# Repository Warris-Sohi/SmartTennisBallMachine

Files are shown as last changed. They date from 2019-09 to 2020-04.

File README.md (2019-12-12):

# SmartTennisBallMachine
warris-sohi.github.io/SmartTennisBallMachine
## Table of Contents
[Introduction](https://github.com/Warris-Sohi/SmartTennisBallMachine#Introduction)

[Build Materials](https://github.com/Warris-Sohi/SmartTennisBallMachine#Materials-Required)

[Time Commitment](https://github.com/Warris-Sohi/SmartTennisBallMachine#Time-Commitment)

[Quick Links](https://github.com/Warris-Sohi/SmartTennisBallMachine#Quick-Links) 

[Testing the acquired materials](https://github.com/Warris-Sohi/SmartTennisBallMachine#Step-1-Test-the-acquired-materials)

[Testing the breadboard prototype.](https://github.com/Warris-Sohi/SmartTennisBallMachine#Step-2-Testing-the-breadboard-prototype)

[Build a PCB prototype](https://github.com/Warris-Sohi/SmartTennisBallMachine#Step-3-Build-a-PCB-prototype)

[Lasercut case and Assembling](https://github.com/Warris-Sohi/SmartTennisBallMachine#Step-4-Project-Enclosure)

[Production Testing](https://github.com/Warris-Sohi/SmartTennisBallMachine#Step-4-Project-Enclosure)

[Conclusion](https://github.com/HusnalK/Resistor-Value-Recognizer-RVR#Conclusion)
## Introduction
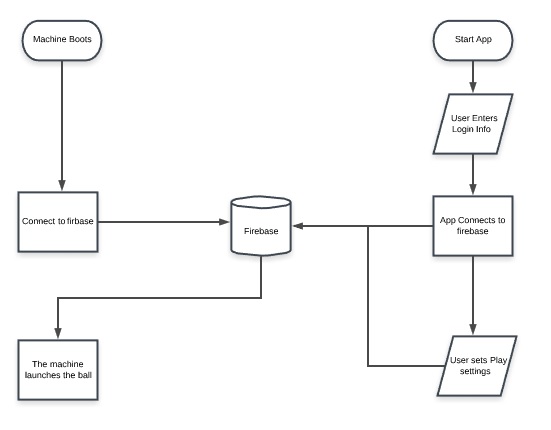
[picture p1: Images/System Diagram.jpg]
System Diagram

##### These instructions are provided to build a launcher for a smart Ping Pong Machine that connects to an app using Firebase to control the aim and speed of ball launched to play. The machine uses a Raspberry 4 Model B as it's development platform, and Sparkfun TB6621FNG driver to control the speed of the 2 DC motors to launch the ball.
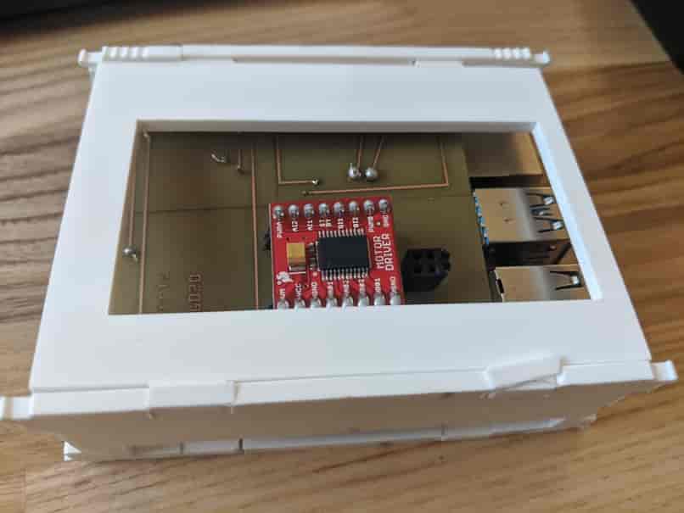
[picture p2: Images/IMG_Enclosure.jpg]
Final Product

##### These build instructions will show you how to program your Pi and build a PCB to mount the Driver and the motors. It also gives you the schemetics to build a laser-cut case to protect the Pi, the PCB and a holder for the DC motors for that can be attached to a base that is connected another component that uses a Servo  Motor to aim the ball horizontally.
## Materials Required
##### 1 - Raspberry Pi 4 Model B Kit
##### 1 - TB6621FNG Dual Motor Driver
##### 2 - Model R360 DC motors
##### 1 - 6V - 9V Power Supply 
##### 2 - 1X20 Female Socket Headers, 1X8 Female Socket Headers
##### 3 - 1X2 Female Socket Headers
## Time Commitment 
##### Materials Testing - 40 Minutes
##### Building BreadBoard prototype - 30 Minutes
##### PCB Etching and Cutting - 60 Minutes
##### PCB Soldering - 45 Minutes
##### PCB Pwer-Up - 15 Minutes
##### Laser Cutting Case - 20 Minutes
##### Case and PCB Assembly - 20 Minutes
##### Final Prototype Assembly - 30 Minutes
##### Total Time Commitment - 4 Hours 20 Minutes
##  Quick Links
##### [Firmware Code](https://github.com/Warris-Sohi/SmartTennisBallMachine/blob/master/Firmware/tbfng6621.py) 
##### [Fritzing File](https://github.com/Warris-Sohi/SmartTennisBallMachine/raw/master/Electronics/DualMotorDriver.fzz)
##### [Laser Cut Model](https://github.com/Warris-Sohi/SmartTennisBallMachine/raw/master/Mechanical/enclosure%20new.cdr)
## Build Instructions
### Step 1 Test the acquired materials
##### After setting up your Raspberry Pi 4, use a basic python GPIO code to test the output for all you pins for your pi.
##### Test the motor driver by checking that all 3 grounds are connected to each other, and check the connection between VCC to GND, External Power input to GND and PWMA/PWMB to GND.
##### The DC motors can be tested using a small current and voltage input.
##### Check the voltage out put from the power supply.
### Step 2 Testing the breadboard prototype.
##### Then the Connect the motor driver, the DC motors and external power supply on a bread board according to the circuit below and in the given fritzing file. to test them using the code provided.
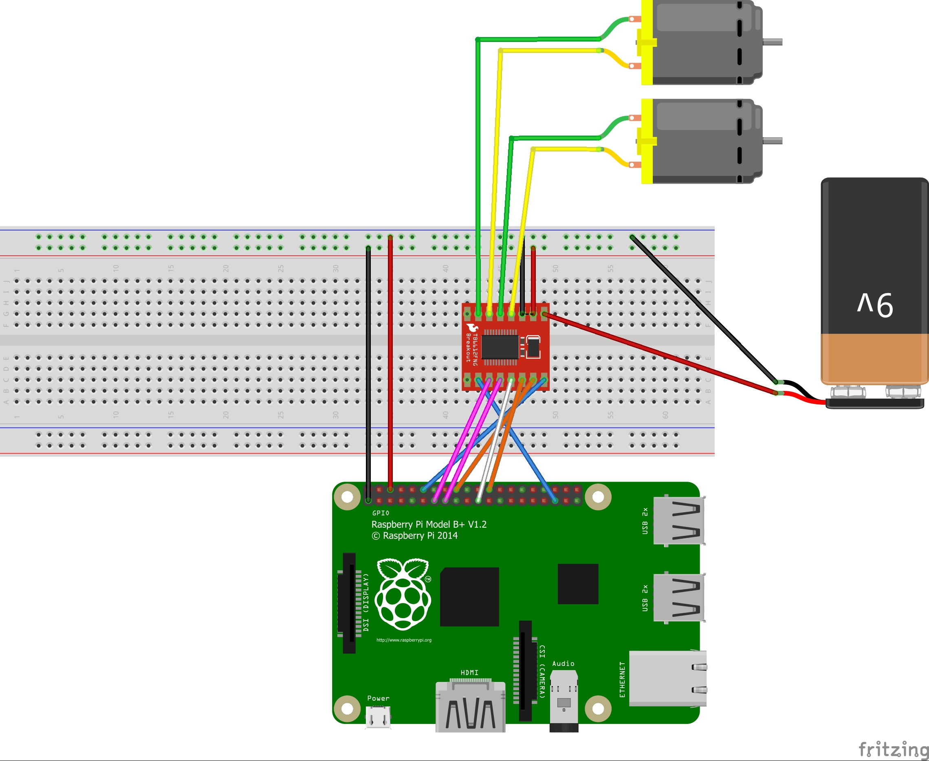
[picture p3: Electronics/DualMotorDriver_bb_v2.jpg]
Bread Board Design

### Step 3 Build a PCB prototype
##### Build printed circuit provided in the Fritzing file, example given below.
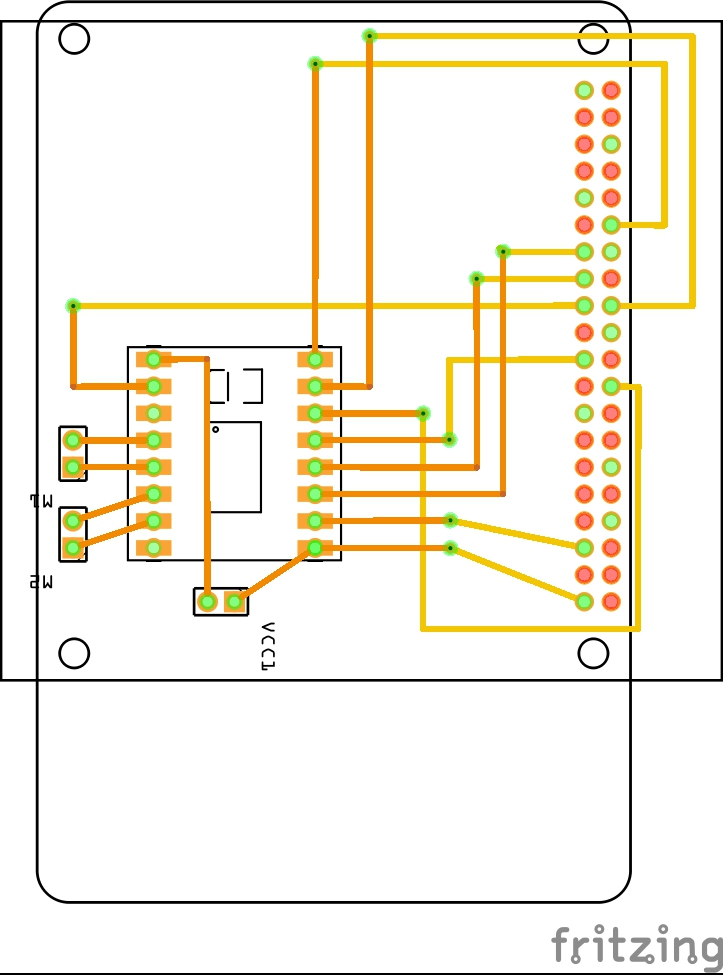
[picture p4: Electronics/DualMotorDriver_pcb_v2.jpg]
PCB Design

##### Use the 1X20 female socket headers and solder them at the bottom of the PCB for the. To mount the PCB on the Raspberry Pi
##### solder the 1X8 and 1X2 socket headers at the top of the PCB to mount the driver and to connect the motors and external power supply respectively.
##### Then test the connections in the PCB, that they are not broken, or are not connected to wrong pins.
##### Then mount the driver on the PCB and the PCB onto the pi 
### Step 4 Project Enclosure
##### The provided .cdr file consists of a case for the Raspberry Pi and mounted PCB and a holder for the DC motors to hold them at required distance so that a ping pong ball can be fit in them and launched. 
##### After enclosure pieces are laser-cut, some of affixes for the Pi case and the DC motors need to shaved off, so that the we can attach them firmly, without needing glue and remove them after, if needed.
## Production Testing
##### When mass-producing this project, steps like making the breadboarding isn't necessary for all the units to be made. The components used are mass produced so, testing individual components can be skipped. This makes production easier and faster. Then you can go straight to testing the connections for th PCB.
## Conclusion 
##### Hence, This project can be reproduced massively.  This is a fairly basic project and can be adjusted to other developer's needs.

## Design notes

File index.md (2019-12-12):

---
tagline: Website with GitHub Pages
description: Simple website with GitHub Pages
layout: page
title: Smart Tennis Ball Machine
---

Gurwarris's Team.
-------------
## December 12, 2019
I have posted my complete [Build Instructions](https://github.com/Warris-Sohi/SmartTennisBallMachine/blob/master/README.md)
My final Product, my PCB has been tested, my closure fits and accomodates my PCB with mounted driver.
My Final Product
## November 28, 2019
[My presentation](https://github.com/Warris-Sohi/SmartTennisBallMachine/blob/master/Documentation/Presentation%20Ping%20Pong%20Machine.pptx)
I have tried laser cutting my enclosure, but it is not upto scale, with my design.

### November 21, 2019
The laser cut design for my enclosure is in .cdr files
[File](https://github.com/Warris-Sohi/SmartTennisBallMachine/blob/master/Mechanical/enclosure%20new.cdr)

### November 21,2019
[3-d Print Enclosure base .stl file](https://github.com/Warris-Sohi/SmartTennisBallMachine/blob/master/Mechanical/Pi%20Enclosure%20Base.stl)
[3-d Print Enclosure lid .stl file](https://github.com/Warris-Sohi/SmartTennisBallMachine/blob/master/Mechanical/Pi%20Enclosure%20Lid.stl)
### November 14, 2019
I realised I was using a wrong port in my pcb. I was supposed to use pin 35, instead I used pin 37. So I created a new PCB design with correct ports.
My Firmware code runs through the 3 different shots I purposed. Straight, backhand and fronthand using the firmware code update below.

#### My PCB design
PCB Design
#### My Breadboard Design
Breadboard Design
My Raspberry pi 4 got short circuited today by my own mistake, I have a lifetime warranty for it. So it will be replaced. Meanwhile I am borrowing my friend's raspberry pi 3 to test my breadboarded circuit and it works.
 
 The [code](https://github.com/Warris-Sohi/SmartTennisBallMachine/blob/master/Firmware/tbfng6621.py) with 3 different modes.
 1. Both motors runnning at same speed 
 2. Motor B running at almost half the original speed
 3. Motor A running at almost half the original speed

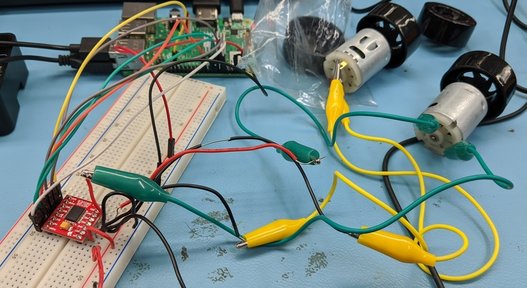
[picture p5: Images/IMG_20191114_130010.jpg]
Circuit working
 

### October 10, 2019
#### Fritzing File
This is the link to my [Fritzing File](https://github.com/Warris-Sohi/SmartTennisBallMachine/blob/master/Electronics/DualMotorDriver.fzz)
#### My Breadboard Design
Breadboard Design
#### My Circuit Schematics
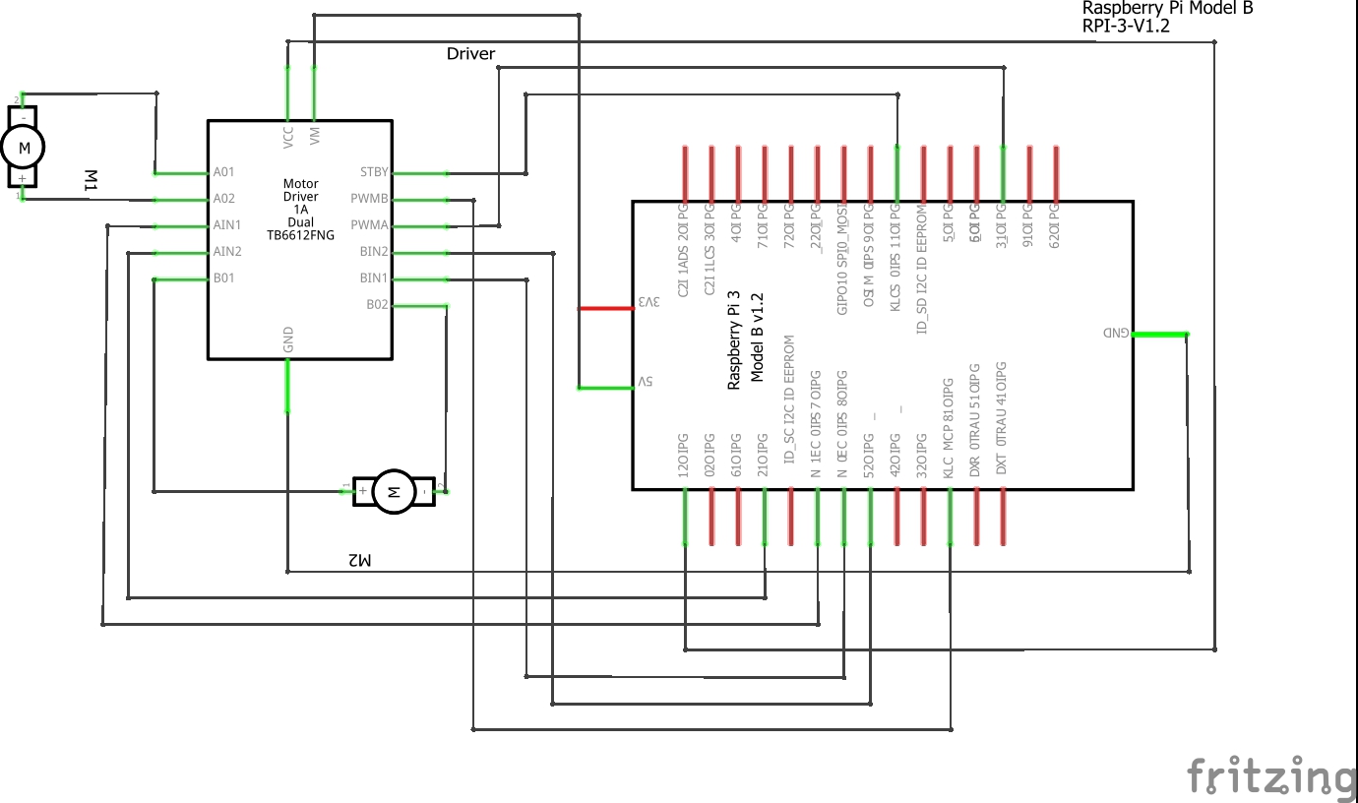
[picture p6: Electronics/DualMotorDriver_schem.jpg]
Circuit Schematics

#### My PCB design
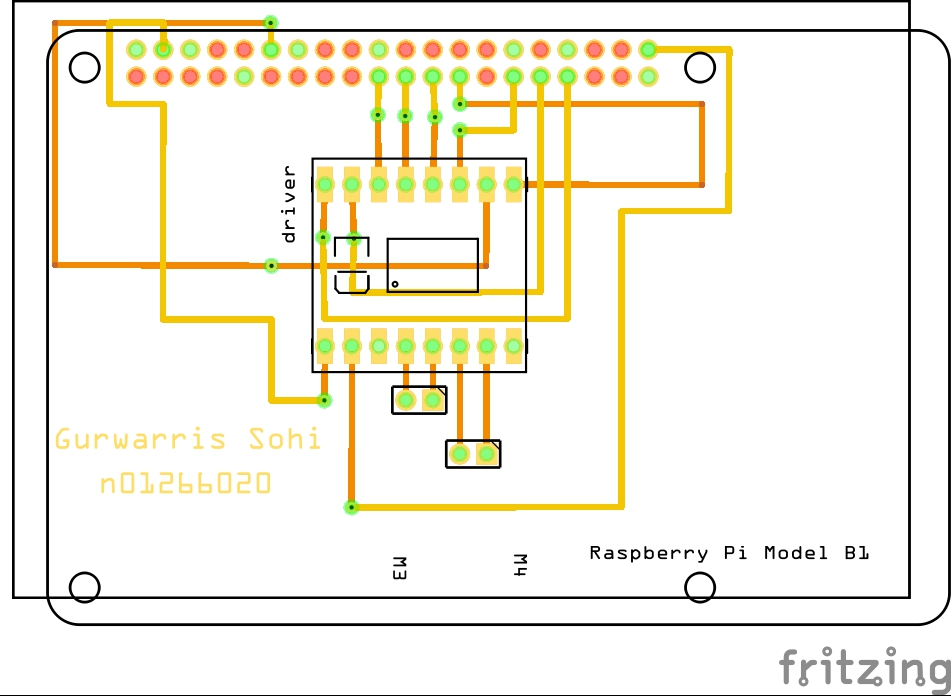
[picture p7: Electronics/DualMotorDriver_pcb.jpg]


### October 10, 2019
My development platform has arrived.
My motors driver has arrived.

### September 26, 2019
Proof of Purcahse
#### My Raspberry Pi 4 Model B is Arriving Today.
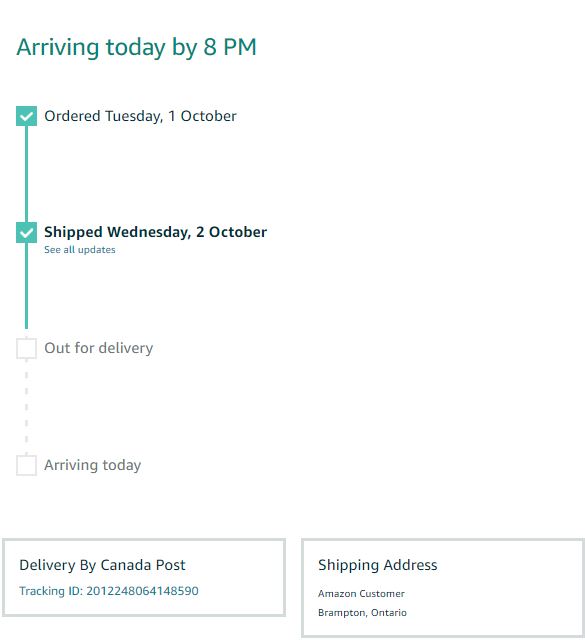
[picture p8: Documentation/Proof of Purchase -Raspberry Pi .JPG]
Proof Purchase Raspberry Pi

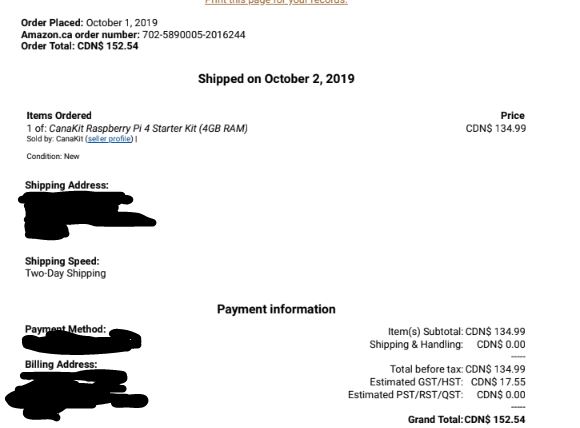
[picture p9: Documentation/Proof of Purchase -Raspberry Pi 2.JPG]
Proof Purchase Raspberry Pi


#### I have already acquired Model R360 DC motors
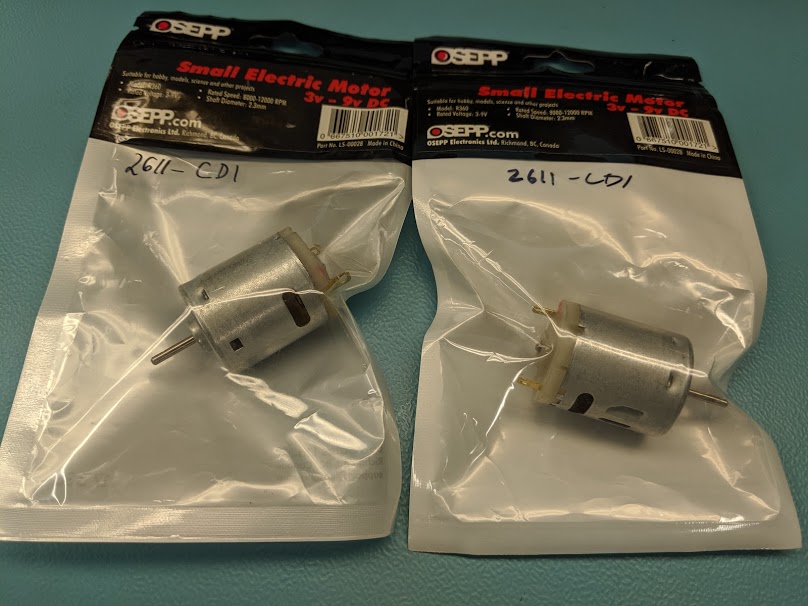
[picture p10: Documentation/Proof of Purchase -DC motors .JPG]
Proof Purchase DC motors


#### I have ordered the Sparkfun Dual Motor Driver
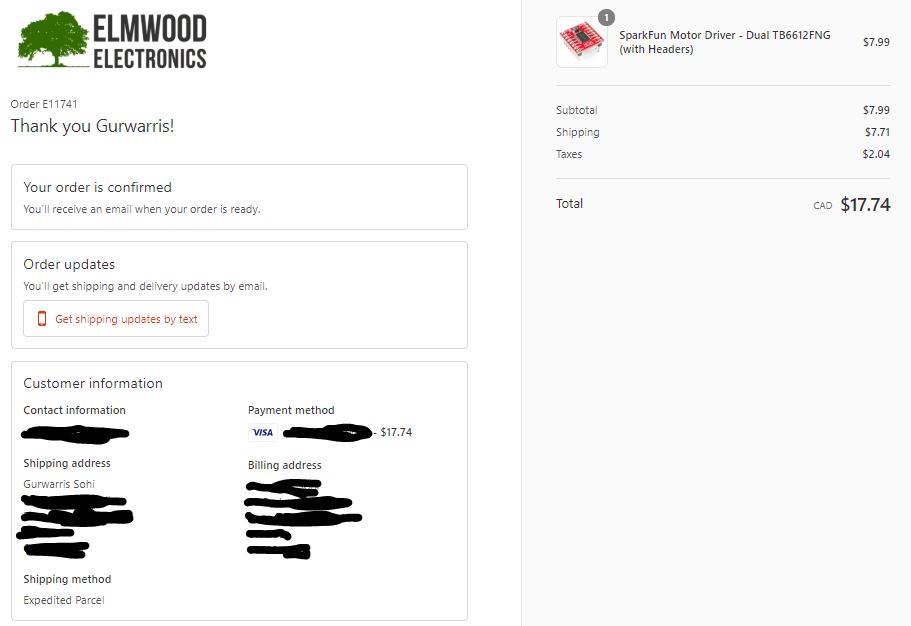
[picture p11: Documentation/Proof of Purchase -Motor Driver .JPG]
Proof Purchase Motor Driver


### September 26, 2019
Today I completed my [Budget](https://github.com/Warris-Sohi/SmartTennisBallMachine/blob/master/Documentation/Project%20Budget.pdf) 

### September 19, 2019

Created [project schedule](https://github.com/Warris-Sohi/SmartTennisBallMachine/blob/master/Documentation/ScheduleCapstone%20Project.pdf).  
### September 12, 2019

Created [proposal](https://github.com/Warris-Sohi/SmartTennisBallMachine/blob/master/Documentation/ProposalContentGurwarrisSohiSmartTennisBallMachine.docx).

### September 5, 2019

Created [repository](https://github.com/Warris-Sohi/SmartTennisBallMachine).

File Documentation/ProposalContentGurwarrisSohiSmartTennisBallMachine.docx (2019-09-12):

43720

Proposal for the development of Smart Tennis Ball Machine

Prepared by Gurwarris Sohi, Sahil Sahil, and Nicolas Cristiano
Computer Engineering Technology Students
https://github.com/Warris-Sohi/SmartTennisBallMachine

Executive Summary

As a student in the Computer Engineering Technology program, I will be integrating the knowledge and skills I have learned from our program into this Internet of Things themed capstone project. This proposal requests the approval to build the hardware portion that will connect to a database as well as to a mobile device application. The internet connected hardware will include a custom PCB with the following sensors and actuators Infrared Sensors, Motion Sensors, Servomotors, Stepper motors. The database will store Our databases will keep the parameters for each play-type or practice session.. The mobile device functionality will include The app is gonna be able to set individual parameters, you can save your level of play (level of difficulty). Our just choose one of our presets for difficulty of play. and will be further detailed in the mobile application proposal. I will be collaborating with the following company/department Startup Life. In the winter semester I plan to form a group with the following students, who are also building similar hardware this term and working on the mobile application with me Gurwarris Sohi, Sahil Sahil, and Nicolas Cristiano. The hardware will be completed in CENG 317 Hardware Production Techniques independently and the application will be completed in CENG 319 Software Project. These will be integrated together in the subsequent term in CENG 355 Computer Systems Project as a member of a 2 or 3 student group.

Background

The problem solved by this project is Tennis ball machines today are costly and in the age where every aspect of our life can be remotely controlled from a mobile device, tennis ball machines are still stuck with buttons and 8 bit displays. Present machines are more hardcoded and way less autonomous than today's standards.. A bit of background about this topic is Tennis ball machines us a container filled with a number of balls (100 balls by present standards), and then some machine use pressure to launch the ball and at the end a pair of tires placed on either side of the ejection tube either horizontally or vertically to finally launch the ball give the needed spin for each serve type. The whole contraption at the end is moved and horizontally and vertically to aim the ball trajectory. This part only affects the elevation and direction of the ball. But a ball can have same max height and distance with different elevations, with different launch speeds..

Existing products on the market include [1]. I have searched for prior art via Humber’s IEEE subscription selecting “My Subscribed Content”[2] and have found and read [3] which provides insight into similar efforts.

In the Computer Engineering Technology program we have learned about the following topics from the respective relevant courses:

- Java Docs from CENG 212 Programming Techniques In Java,
- Construction of circuits from CENG 215 Digital And Interfacing Systems,
- Rapid application development and Gantt charts from CENG 216 Intro to Software Engineering,
- Micro computing from CENG 252 Embedded Systems,
- SQL from CENG 254 Database With Java,
- Web access of databases from CENG 256 Internet Scripting; and,
- Wireless protocols such as 802.11 from TECH152 Telecom Networks.

This knowledge and skill set will enable me to build the subsystems and integrate them together as my capstone project.

Methodology

This proposal is assigned in the first week of class and is due at the beginning of class in the second week of the fall semester. My coursework will focus on the first two of the 3 phases of this project:
Phase 1 Hardware build.
Phase 2 System integration.
Phase 3 Demonstration to future employers.

Phase 1 Hardware build

The hardware build will be completed in the fall term. It will fit within the CENG Project maximum dimensions of 12 13/16" x 6" x 2 7/8" (32.5cm x 15.25cm x 7.25cm) which represents the space below the tray in the parts kit. The highest AC voltage that will be used is 16Vrms from a wall adaptor from which +/- 15V or as high as 45 VDC can be obtained. Maximum power consumption will be 20 Watts.

Phase 2 System integration

The system integration will be completed in the fall term.

Phase 3 Demonstration to future employers

This project will showcase the knowledge and skills that I have learned to potential employers.

The brief description below provides rough effort and non-labour estimates respectively for each phase. A Gantt chart will be added by week 3 to provide more project schedule details and a more complete budget will be added by week 4. It is important to start tasks as soon as possible to be able to meet deadlines.

We are planning our machine on a Raspberry Pi 3, which will controll the servo motors that laungh the ball, and also the stepper motors that will aim the ball accordingly and motion sensors to modulate ball speed.

Concluding remarks

This proposal presents a plan for providing an IoT solution for Our machine is based on a simpler design than the present machine, which will make the machine cost effective and when the machine is connected to the app, most of the processing is done on the mobile side. So we can have smaller processing size on the machine.. This is an opportunity to integrate the knowledge and skills developed in our program to create a collaborative IoT capstone project demonstrating my ability to learn how to support projects such as the initiative described by [3]. I request approval of this project.

References

[1] Baldwin, D. M. (1977). Using the tennis ball serving machine. The Physics Teacher, 15(7), 432–434. doi: 10.1119/1.2339719,5. Understanding the Motion of the Ball (Ball Trajectories). (n.d.). Tennis Science for Tennis Players. doi: 10.9783/9780812201468.72,

[2] Institute of Electrical and Electronics Engineers. (2015, August 28). IEEE Xplore Digital Library [Online]. Available: https://ieeexplore.ieee.org/search/advsearch.jsp

[3] N/A

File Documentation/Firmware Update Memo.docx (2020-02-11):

TO: Kristian Medri, Professor, Humber College School of Applied Technology

FROM: Gurwarris Singh Sohi, Computer Engineering Technology Student

Cc: Nicolas Cristiano and Shubham Sharma

DATE: February 4th, 2020

SUBJECT: Ping-Pong Machine Firmware/Image Status

Respected Sir,

Here is a progress update for the development of the firmware for the Smart Ping-Pong Machine.

The firmware is currently being developed on a Raspberry Pi 4. The development platform is running on the Raspian OS and it is programmed in python language. The IDE being used for this development is ThonnyPython. The image of Raspian being used for the development was the one provided by Humber College. It has been set up to allow remote access, using an Ethernet cable and Ethernet-USB adapter to connect to any PC or laptop. The Raspian OS image has been configured to allow remote access and can be accessed using CLI with Putty and using GUI with VNC viewer. The firmware is developed to control the Servo motor, the solenoid and Dual DC motor driver. The code for firmware is now an integrated version of the base code for the prototypes for the given devices. The new firmware was developed using the code for the dual motor driver as base. The present version is not setup to get the play difficulty values stored in the firebase by the mobile application. But in the present version of the code play settings are hard-coded in the code and for a later version, a defined function can be added to get the values from the firebase periodically and use them to run the devices to provide a play level according the settings set by the user. The firmware uses the GPIO and time module from the Raspberry Pi python modules. The GPIO module functions are used to use the In/Out pins of the Raspberry Pi in BOARD setting. During the initial setup, 5V outputs are set to turn on the VCCs for the motor driver and the Servo motor. Also, GPIOs used for the Motor Driver logic and the Solenoid are set to output and the 3 PWM outputs to control the Servo motor and the two DC motors. The PWMs are setup to output a 100Hz frequency to provide easy calculation for the value of Duty Cycle needed for favorable physical output from the DC motors and the Servo motor. After the setup is completed by making sure that the GPIOs that control the motors and the solenoid are set to the values of HIGH and LOW as needed to set the solenoid in position and the directions for the motors are set. There are different functions defined to simulate the different shots for the Ping-Pong ball, serve up the ball at the given intervals and turn the machine at a variable angle. The firmware runs in a loop to systematically and periodically, serve up the ball then launch the ball straight. Then the loop runs while turning the angle periodically and alternating between the straight shot, top spin and back spin shots. The angle variation is random, ranging between zero to fifty degrees. For the upcoming version, the defined function needs to be implemented that periodically updates the currently hard-coded values for angle, interval and difficulty.

Thanks for reading the content of our firmware update. Here are the links to the various firmware codes for your perusal.

GitHub link to the Motor Driver Firmware code:

https://github.com/Warris-Sohi/SmartTennisBallMachine/blob/master/Firmware/motor%20driver.py

GitHub link to the Solenoid Firmware code:

https://github.com/Warris-Sohi/SmartTennisBallMachine/blob/master/Firmware/solenoidP.py

GitHub link to the Servo Motor Firmware code:

https://github.com/Warris-Sohi/SmartTennisBallMachine/blob/master/Firmware/code.py

GitHub link to the integrated Firmware code:

https://github.com/Warris-Sohi/SmartTennisBallMachine/blob/master/Firmware/tbfng6621.py

Sincerely,

Gurwarris Singh Sohi

# Rubric:

Status

/1 Hardware present?

/1 Memo by student B + How did you make your Image/firmware? (500 words)

/1 Code can be run via serial or remote desktop

/1 Wireless connectivity

/1 Sensor/effector code on repository

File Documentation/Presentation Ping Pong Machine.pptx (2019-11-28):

## Ping Pong Machine

Gurwarris singh sohi

## Introduction

- Objective: Make a cost effective ping pong machine.
- Problem: No speed modulation and use more hardware to launch.
- Explanation: The original machine uses a pair of motors set a constant speed and servo /or stepper motors to aim the balls.
- Solution: Use PWM controlled DC motors, to launch ping pong balls at variable speeds and angles.
- Explanation: My design uses PWM to alter launch speed at any time. It also allows me to modulate the speed of either motor so, a difference in the speed of the motors allow me to launch balls at variable angles, without using servo /or stepper motors.

## Budget

- Raspberry 4 Model B (extra cost) + CDN$ 152.54
- HDMI to VGA adapter (extra cost) + CDN$ 22.59
- DC motors (extra cost) + CDN$ 12.73
- TB6612FNG (extra cost) + CDN$ 17.74
- Shipping/Delivery (no extra cost or already included) + CDN$ 0.00

## Schedule

- Breadboard Design
  - Setback: I made a mistake in using a port, and while testing, I thought my code had a bug.
- PCB Design
  - Setback: The earlier setback costed me my first PCB. I had to design, print and solder a whole new PCB, which led to a schedule setback.
- Enclosure
  - Setback: My first enclosure was designed just to hold Raspberry Pi, but the mounted driver PCB didn’t fit in. Had to create a new one.

## Prototype Hooked Up

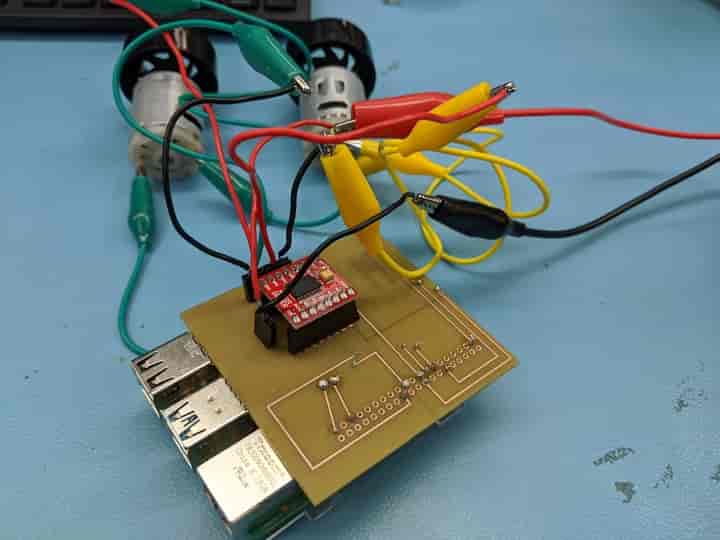
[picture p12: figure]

## Previous Course Knowledge

- TECH 103 Digital Fundamentals - Logic Design
- TECH 101 Electric Circuits + TECH 150 Electronic Devices and Circuits - Lab equipment and safety precautions
- TECH 150 Electronic Devices and Circuits – Soldering
- CENG215 Digital and Interface Systems – Controlling a DC motor with PWM
- CENG252 Embedded Systems - Programming on Raspberry Pi
- https://learn.sparkfun.com/tutorials/tb6612fng-hookup-guide/all

## Thank You

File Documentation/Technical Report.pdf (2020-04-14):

# Smart Ping Pong Ball Machine

From: Name - Gurwarris Singh Sohi Discipline: Computer Engineering Technology Date: 14 January, 2020

## Declaration of Joint Authorship

We, Gurwarris Singh Sohi, Nicolas Cristiano, and Shubham Sharma, confirm that this

work submitted is the joint work of our group and is expressed our own words. Any

uses made within it of the works of any other author, in any form (ideas, equations,

figures, texts, tables, programs), are properly acknowledged at the point of use. A list of

the references used is included. The work breakdown is as follows: Each of us provided

functioning, documented hardware for a sensor or effector. Gurwarris provided the

functioning for a TB6621FNG Dual Motor Driver. Nicolas Cristiano provided the

functioning for a SG90 micro Servo Motor. Shubham sharma provided functioning for

ROB11015 Solenoid . In the integration effort Nicolas Cristiano is the lead for further

development of our mobile application, Gurwarris Sohi is the lead for the Hardware, and

Shubham Sharma is the lead for connecting the two via the Database.

## Proposal

We have created a mobile application, worked with databases, completed a software

engineering course, and prototyped a small embedded system with a custom PCB as

well as an enclosure (3D printed/laser cut). Our Internet of Things (IoT) capstone project

uses a distributed computing model of a smart phone application, a database

accessible via the internet, an enterprise wireless (capable of storing certificates)

connected embedded system prototype with a custom PCB as well as an enclosure (3D

printed/laser cut), and are documented via this technical report targeting OACETT

certification guidelines.

Intended project key component descriptions and part numbers

Development platform: Raspberry Pi 4 B+

Servo Motor SG90: Used to adjust the horizontal rotation of the ping-pong machine

TB6621FNG Motor Driver: Used to adjust the launch speed of the machine in addition

to its vertical launch properties

ROB 11015 5V Pull Solenoid: Used to control the time interval between balls launching

We will continue to develop skills to configure operating systems, networks, and

embedded systems using these key components to cooperate with one another so they

can be integrated into a fully functional ping-pong machine in addition to the ping-pong

Smartphone application.

Our application will contain several play options to optimize the amount of success the

player will have in being able to develop their skills, including adjustable difficulty,

launch interval and horizontal launch. The application will also allow the user to save and access the user’s settings from the last 30 play sessions. These settings are stored

into the application’s database after each session has ended.

During the play session, when the ball enters the machine, the solenoid will pull in the

ball for however long the user has set the time interval for. Once the ball has launched,

it will be able to get launched horizontally within a 180 degree radius, while the difficulty

will determine the ball’s launch speed and elevation.

Our project description/specifications will be reviewed by Sebastien Dwornik, ideally an

employer in a position to potentially hire once we graduate. They will also ideally attend

the ICT Capstone Expo to see the outcome and be eligible to apply for NSERC funded

extension projects. This typically means that they are from a Canadian company that

has been revenue generating for a minimum of two years and have a minimum of two

full time employees.

The small physical prototypes that we build are to be small and safe enough to be

brought to class every week as well as be worked on at home. In alignment with the

space below the tray in the Humber North Campus Electronics Parts kit the overall

project maximum dimensions are 12 13/16" x 6" x 2 7/8" = 32.5cm x 15.25cm x 7.25cm.

Keeping safety and Z462 in mind, the highest AC voltage that will be used is 16Vrms

from a wall adapter from which +/- 15V or as high as 45 VDC can be obtained.

Maximum power consumption will not exceed 20 Watts. We are working with prototypes

and that prototypes are not to be left powered unattended despite the connectivity that

we develop.

## Executive Summary

Our team has worked towards, creating an affordable and competitive Ping Pong Ball

machine. This project was started with comparing the various Ping Pong Ball machines

in the market currently. The common observation was that the machines present in the

market right now are either too expensive or don’t give you much competitive play

features. Our Smart Ping Pong ball machine will incorporate a feasible product that

allows a user to play at various difficulties, with the new smart features like database

and statistic support and be controlled by an app run on any android device. This

machine will achieve complex play settings using minimal and cheaper hardware but,

also using smart and intricate firmware. Using less and cheaper hardware allows us to

keep the cost down, and compete with currently sold machines in the market. To make

manufacturing easier, we can sell the product in the form an assembly kit to keep the

manufacturing costs low. Even if, the cost is low, this product can compete with the

most competitive and expensive products in the market.

## Contents

## List of Figures

Figure 1. By Android Studio - https://developer.android.com/studio/, CC BY-SA 4.0,

https://commons.wikimedia.org/w/index.php?curid=74094999 | 19

Figure 2. Initial schematic. This work is a derivative of "http://fritzing.org/parts/" by

Fritzing, used under CC:BY-SA 3.0 | 20

Figure 3. This work is a derivative of "http://fritzing.org/parts/" by Fritzing, used under

CC:BY-SA 3.0 | 20
Figure 4. Breadboard prototype | 21

Figure 5. PCB design This work is a derivative of "http://fritzing.org/parts/" by Fritzing,

used under CC:BY-SA 3.0 | 22
Figure 6. Humber Sense Hat Prototype PCB | 22
Figure 7. Example enclosure | 23

## 1.0 Introduction

Our project involves creating a Smart Ping-Pong machine that includes a wide array of

play options to allow for a wide range of playing styles. This will allow for players of

different skillsets to improve on their ping-pong abilities in a fun and varied manner. In

the playing application, the user can select their ideal play preferences to give them a

comfortable play experience or to ease them into using the machine. These settings

include: play difficulty, organized into easy, medium, and hard categories which affects

both the launch speed and the types of shots the machine is able to perform; easy

difficulty provides forehand and backhand shots at the standard elevation, whereas the

hard difficulty provides the prior 2, in addition to the topspin and backspin shots at

random elevations; launch angle, which changes the horizontal launch of the ping-pong

ball within a 45-degree radius; and the launch interval which affects the amount of time

balls launch between one another, which range from 0.3 to 5 seconds. Our playing

application involves a series of databases that allow the player to save and record the

fields for the play options of their past play sessions. After 30 sessions have already

been input, any new sessions will gradually override the old ones to give the player a

better idea of their progress using the machine. The range of elevations the balls launch

depends on the difficulty set. It will be set at a permanently neutral elevation if set to

easy but will fluctuate if set to a higher difficulty. In terms of scope, first we need to

create a hardware prototype and then test for errors to evaluate if we need to change

anything for the refined version. Afterwards, we need to create the Firebase databases,

which will act as the bridge between the play application and the hardware. The default

settings of the play application are set to a launch angle of 5-degrees, a time interval of

5 seconds and an easy difficulty setting. However, the database will be able to transfer

the settings of the user’s last play session to their current one, in order to make for a

more efficient play experience. Schedule-wise, we plan on building our firmware and

application first. We will then develop our databases, which connect to the firmware and

application. Lastly, we will develop the enclosure for the machine, which includes the

structure for the device and the piping from where the ball launches.

1.1 Scope and Requirements

It is an Internet of Things (IoT) capstone project that uses a distributed computing model

of a smart phone application, a database accessible via the internet, an enterprise

wireless (capable of storing certificates) connected embedded system prototype with a

custom PCB as well as an enclosure (3D printed/lasercut), and is documented via an

OACETT certification acceptable technical report. This project will use a database

hosted by Firebase which connects the mobile application to the machine. The machine

hardware is developed around a Raspberry Pi 4 Model B which can connect to a

wireless connections using enterprise wireless certificates. The Raspberry Pi also

support good memory and processing power to be able to support multi-threading to

control multiple components of the machine. The Pi outputs multiple PWMs and GPIOs

to control a Servo Motor SG90 to aim the ball, TB6621FNG that control 2 9V DC motors

to launch the ball and Pull type Solenoid to prevent multiple balls to be launched from

being launched in a hectic way.

## 2.0 Background

We would like to thank our mentor Sebastian Dwornik from PDA for supporting this

project. He has been instrumental in accomplishing our ideas and hopes for this project

by providing support in terms of sorting through our ideas giving them objective

approaches, helping with the design for the app and the hardware. Our idea was based

after reviewing the designs and features of some of the available machines in the

market. The current devices available are either too costly or provided minimal features

(13 Best Ping Pong Robots That Will Improve Your Game Instantly, 2020). These

machines are all controlled using some connected basic remote and in the age where

people control everything in their households using smart switches and mobile

applications (Pathan, 2019), why limit this machine to such old methods. Also,

connecting the machine with the app and the database will help the user track their

progress as they continue to use their machine from beginner to advanced player.

Every professional player likes to keep track of their progress/status and this idea has

been incorporated with training new players at a young age/beginners (Sumich, 2013).

So this machine can be used to help such beginners and help save them some money

to provide such training and features at a minimal cost. The more expensive machines

available in the market support some different shot types but are unable to change them

continuously during a single play though. This machine aims to change that and give

highly random shot types to simulate the difficulty of an actual match. To complete this

project we have learned how to create android applications in our software production

class. We have also learned how to test and create a hardware prototypes for the

components of the machine inclusive with a firmware and enclosure for the development platform and the components use in our hardware project class. We have

also learned how to create and handle json based databases hosted by Firebase and to

Read, write and update them using the applications we create in our software

production class. We have already created and presented some hardware prototypes

incorporating our individual components for the machine and now we will integrate them

to create the refine prototype that can be controlled and operated through the a

Firebase database.

## 3.0 Methodology

This project is called Smart Ping Pong Ball machine, which controls our prototype using

our mobile application. The design for hardware uses simple hardware components with

a firmware developed on a Raspberry Pi 4 Model B.

3.1 Required Resources

3.1.1 Parts, Components, Materials

When constructing the circuit for our individual projects, it was expected that we use of

Breadboards first to troubleshoot for any potential errors. Afterwards, we had to

implement our designs onto PCB’s which would then connect to a circuit board, the

Raspberry Pi 4. 40-pin outputs were used in all circuits to directly connect the PCB’s

onto the Pi’s. An SD card and SD card adapter were used to transfer data and files from

the computer directly onto the Pi to allow the Pi to operate properly. An Ethernet cable

and a USB-to-Ethernet cable were required to connect the Pi’s directly to the

computers, which allowed software such as Raspian to be activated and us to remote

access it for its GUI and CLI. 3 millimeter acrylic cases were used to encapsulate our

hardware designs to ensure that everything in the designs stay in place. For the servo

motor design, a 3-pin serial header was used to connect the wires of the servo motor

directly onto the PCB. A 220 ohm resistor and a 2.2 kilo-ohm resistor were also used in

the design to moderate the amount of current that flowed through the design to ensure

the circuit didn’t overheat. Additional packs of both types of resistors were required as

all the remaining ones were damaged during the soldering process. It also included an

NPN transistor to control the flow of the current to allow the Servo Motor to rotate both clockwise and counter clockwise. Finally, an LED was included as a visual way to

confirm that the circuit was properly constructed. For the Solenoid design, another NPN

transistor, a diode and a 2.2k Ohm resistor was used to amplify the current output to the

Solenoid at a low voltage value. The resistor and transistor were used to form the

current amplifier, and the diode was used so to cut-off the current form flowing into both

directions. Female headers were used to mount the PCB onto the Pi and the input wires

to the RB-1011 5V Push-Pull Solenoid onto the PCB. An external 9V power supply was

used to power provide the adequate the voltage for the Solenoid and the TB6621FNG

Dual Motor Diver. The motor driver drives the 2 6 to 12V bidirectional DC motors using

the external power supply and the PWM and GPIO input from the Raspberry Pi 4.

3.1.2 Manufacturing

We all created our PCB’s using Fritzing. Once we finished our designs, we sent the

designs to the prototype lab for them to print out. The printing process usually took a

day from when we sent them the PCB design in gerber file format. During the

construction of the Servo Motor PCB, 4 copies had to be printed for various reasons. In

the initial design, the copper wiring was placed on opposite layers for some

components. As a result, the schematic had to revised to ensure greater design

consistency. The next couple of PCB’s had to be discarded as a result of soldering

complications. As the proper soldering technique had not fully developed, some of the

components were put in poor condition and parts of the copper wiring ended up getting

singed out. This essentially rendered those PCB’s impractical. The final PCB includes a

3-pin serial header, a 40-pin serial header, an NPN transistor, 2 resistors and an LED.

The PCB case for the Servo Motor PCB was made using the Corell software. After the design was made, it was sent to the prototype lab for them to construct using the laser

cutter, which took approximately 20 minutes. This design had to be printed out a few

times to make minor spacing changes to the ports. For the Solenoid, the PCB had to be

printed up to 5 times, because of the fault in the initial design led to some of the

components becoming unusable for the secondary attempts. During the third attempt,

the design was fixed but due to unstable to testing parameters like required minimum

current and maximum voltage limit and lack of knowledge regarding these factors led to

the small components like transistors and diodes being short-circuited. Also, during the

initial design of the PCB using Fritzing, it lacked the components being used which had

to be resolved using similar components for the design. But these components not

being the same ones as the ones to be used had wrong specifications that resulted in

impractical PCB design. The case was laser-cut on black opaque 4mm acrylic. The

design was based on a case for a Raspberry Pi 3 but was edited to support ports and

nodes on the Raspberry Pi 4. For the Dual Motor driver, the PCB was required 3

attempts. The first attempt was rendered useless, because complications while

soldering the sockets on the wrong side of the PCB. The second attempt was the same

design which led to the Raspberry Pi crashing and corrupting its EPROM. The fault was

discovered and fixed during the third attempt and solved which led to the smooth

operation of the DC motors using the TB6621FNG driver. Printing the case for the DC

motors component required multiple attempts. Initial designs were based on a case for

a Raspberry Pi 3 and edited using Inkscape, but the designs created, and cut were not

on scale with design. It took a few tries to figure out how to fix this problem, as it was

discovered that the in-software measurements of the design were scrambled while saving them as .cdr format files. When we used Corel Draw for the design, we were

successful in cutting the case for the Raspberry Pi. Then we created a fixture to hold the

2 DC motors at a fixed distance so that a ping pong ball could be launched through

them. But it took a few recalculations and re-cutting to get the holes just right to hold

them in place.

3.1.3 Tools and Facilities

In order to obtain the PCBs, we had to go to the prototype lab to submit our PCB cases

designed using Fritzing software in gerber file format and receive the actual PCB which

typically took 24 hours. In order to properly solder the various components onto the

PCB’s, soldering stations from the prototype lab and room J 232 were used. The

soldering station consisted of a soldering iron that melted the lead-free soldering wire in

place when a component was placed on top. A de-soldering iron with suction pump was

also available in case a component needed to be taken out or readjusted. After each

solder, a sponge was present to moisten the soldering iron to ensure that no extra

solder was left because it could dampen the heat from the soldering iron. During the

soldering process, we had to use a vent as a safety precaution to ensure that we didn’t

inhale any of the fumes that emitted from the solder. In addition, we had to use safety

glasses when soldering to ensure that the fumes or any stray piece of metal didn’t get in

our eyes. Holders were available to hold the PCBs in place while soldering. We also

used microscopes with flashlights to solder accurately at small and complex joints.

When soldering the PCB for the Servo Motor for the first few times, improper technique

was used, resulting in too much solder getting placed onto the ports, melting parts of the copper wire, and resulting in the boards looking disorganized overall. It took about 4

weeks for this PCB to get soldered properly. When creating a case for the component

prototypes, we used Inkscape and/or CorelDraw to design it and sent it to the prototype

lab in .cdr format for getting laser-cut. We used the datasheets for the Raspberry Pi,

solenoid, servo motor and the motor driver to design the circuits and test them. We had

some tools available to test our circuits and troubleshoot them when any problems

happened. For example, when We had doubts about my circuit and my testing code for

the motor driver, we used the tools like oscilloscope and multimeter to first test the

output from Pi for its GPIOs and PWMs. These same tools where used to troubleshoot

when my Raspberry Pi was shorted by the PCB we had created. We used these

devices to troubleshoot the circuit for the Solenoid circuit. We used VNC viewer and

Putty to remote access our Raspberry Pi’s GUI and CLI modes for development of our

prototype code. We used NOOBS software to load the Raspian OS image onto the SD

card and used Thonny as the IDE to program in python. We are using Firebase to host

the databases for our project and using it was the medium between our mobile

application and the hardware. We used Android Studio to develop our mobile

application written in Java. We also used LinkedIn Learning as a source, to learn

various ways to implement our ideas in the both mobile application and the hardware

prototypes. We used Trello to keep track of our progress and in combination with Slack

that we used to contact and converse with our collaborator Sebastian Dwornik, helped

us share our progress with a more featured and described means.

3.1.4 Shipping, duty, taxes

For the Servo Motor project, everything was ordered off of Amazon Prime with

everything arriving around 1 day after the time of shipment. There weren’t any duty fees

applied to the ordered parts as everything was sourced from Canadian suppliers. There

weren’t shipping fees since everything was ordered through an Amazon Prime

membership. Otherwise, the shipping fees would have been $6.99/shipment. There

weren’t any regular taxes applied to the components, aside from the GST on the

microSD card and Adapter, $1.12 (or 13%) of the initial price, $9.32.

For the Solenoid prototype, everything was ordered from Amazon and everything

arrived within two days of ordering them. As none of the components were shipped from

outside Canada, there were no extra duty charges and all of them were shipped

together, having reached the minimum amount, no shipping charges were added. So

the final invoice was just the price of the components plus the 13% Tax. But after that

some small components had to be reordered and, not having reached the free shipping

threshold, $6.99/shipment for two separate shipments were added with including the

13% HST.

For the Motor Driver prototype, The DC motors and the socket headers were bought

from Sayal Electronics, so no shipping charges. The Raspberry Pi Kit was ordered from

Amazon and having reached the no shipping threshold, only 13% HST was paid. But

the motor driver was ordered from Elmwood Electronics, and including with cost of the

driver, $10.56 shipping charge and 13% HST was paid.

3.1.5 Time expenditure

For Gurwarris’ project, he ordered his dual motor driver from Elmwood Electronics.

When he ordered the component, they didn’t give him an exact delivery date, which

ended up being 3 weeks. However, the male socket headers were already soldered

onto the motor driver upon delivery, saving Gurwarris extra work. The Raspberry Pi kit

was ordered from Amazon and arrived the day after. The kit was a product from

Canakit, which included an already set up SD card with a bootable OS image for a

Raspian. Which saved him some time in the working time setting up and went directly to

development for the firmware code which was tested on the breadboard prototype. It

took me a few hours to design the circuit for both the breadboard and the PCB. Which

took up to 24 hours to print. There were some errors in the PCB that had to be led to

Raspberry Pi being corrupted. So, it had to be printed again and it took some time for

the PCB prototype to function. It took up to four weeks to get the prototype functioning.

Also for the acrylic case, it took me up to 4 attempts to get just my case for the

Raspberry Pi up to the standards and each attempt took about a couple of hours to

edit/fix and 15-30 minutes to cut. The fixture for the motors also took me a whole day of

a continuous process of re-measuring and re-cutting to fit it.

For Nicolas’ project, all of his components from Amazon Prime, each of which took a

day to deliver. The first delivery, consisting of everything aside from the resistors, was in

early October. The second delivery, consisting of the 220 and 2.2 kilo ohm resistor

packs, was in late November. Complications arose from connecting the Pi to the

desktop, which made it difficult to determine if the motor was working properly with the code it was given. It took roughly 5 weeks to determine if the code was working, with an

additional 4 spent designing and soldering the PCB.

For the Solenoid prototype, the components arrived two days after they were ordered

from Amazon. But because of clashing information and some of it being inaccurate for

the circuit to be used. It took me 3 weeks to design the accurate circuit and test it out on

the breadboard. This kind of wasted a lot of my time as the PCBs produced had to be

soldered, but they ended up not only no working, but rendering my components

useless. So we had to order the components again and keep testing the circuit, So the

final PCB prototype was finished in 7 weeks .The case took only a couple of attempts to

polish and fit for my raspberry Pi.

3.2 Development Platform

3.2.1 Mobile Application

Research has shown that tennis players, both new and experienced, are using tennis

ball machines in order to gain experience and develop their abilities in an effective and

efficient manner. Capitalizing on this trend, hardware has been developed for a ping-

pong machine, which works largely in the same manner as a tennis machine, only on a

smaller scale. Software has also been developed for an application that allows the

player to adjust various play factors for how the ping-pong machine operates.

Login Activity

Upon opening the application, the player is required to input their individual data into a

signup page. These fields include:

- First Name
- Last Name
- Email
- Password
- Password Confirmation

There are several parameters that need to be achieved for the user to be able to sign

up. Most significantly, none of the fields are allowed to be empty. The first name and

last name must not have any numbers or special characters (ie ?,!$). The email and

password must not have any spaces in between characters. The password must be eight to sixteen characters, and have at least one lowercase letter, one uppercase

letter, one special character and one number. The password confirmation must match

up perfectly with the password. After the user signs up, they can login for all subsequent

sessions, where they only need to input their email and password.

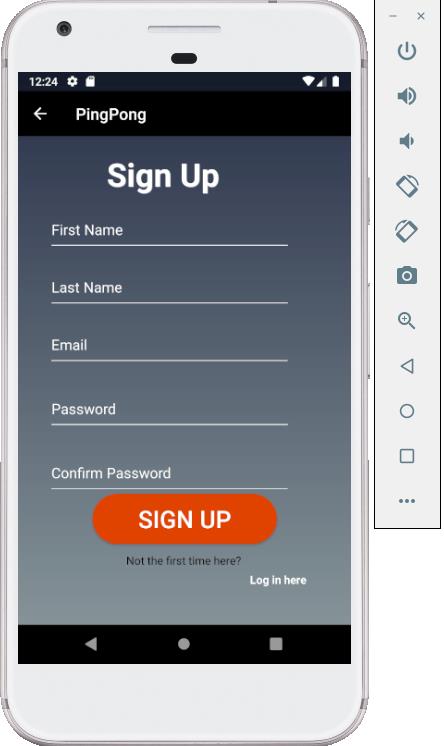
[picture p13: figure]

Figure 1: Sign Up Page

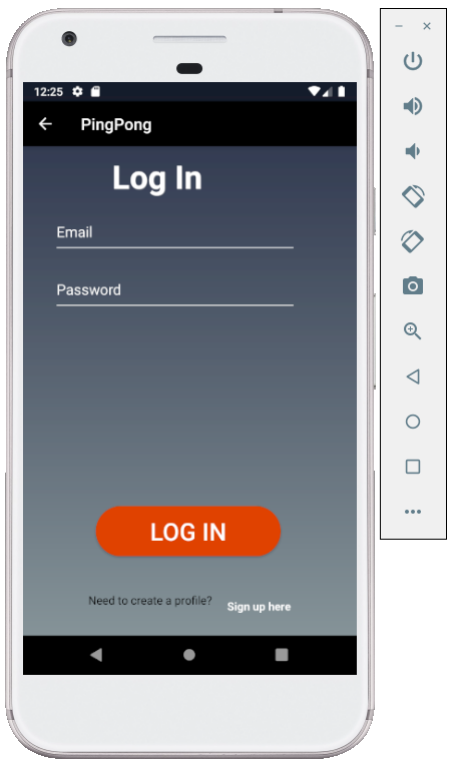
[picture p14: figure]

Figure 2: Login Page

Data Visualization Activity

Once the user logs into the application, they can access a profile page, which displays

their first name, last name, email address and a serial number that denotes what machine the given account is linked to. When the user first logs in, the application’s

database stores what serial number they have. The profile screen also lets the users

access their play settings from the last 30 play sessions.

Action Control Activity

Before the user enters their play session, they can select from a range of play settings.

These settings include:

- Difficulty: easy, medium and hard difficulties are selectable, which impact both

the launch speed, the range of elevations and type or variation of shots the ping

pong balls launch at the user

- Angle: the user can control the horizontal launch angle of the ball from a neutral

center position to a 25 degree range, both left and right of the center.

- Launch Interval: the user can control the time interval the balls launch between

one another. They can choose between 0.3, 1, 2 and 5 seconds.

If the user does not choose any of their individual settings, they are set to default, which

consists of an easy difficulty, a 10-degree launch angle, and 5 second launch interval.

Once the user chooses their settings, they can launch their play session in another

screen. When launched, the application displays a timer that shows the duration of the

play session. If the user wants to change their settings, they need to press the stop button so they can re-access the settings page. They are then able to restart the play

session once everything is adjusted to their liking.

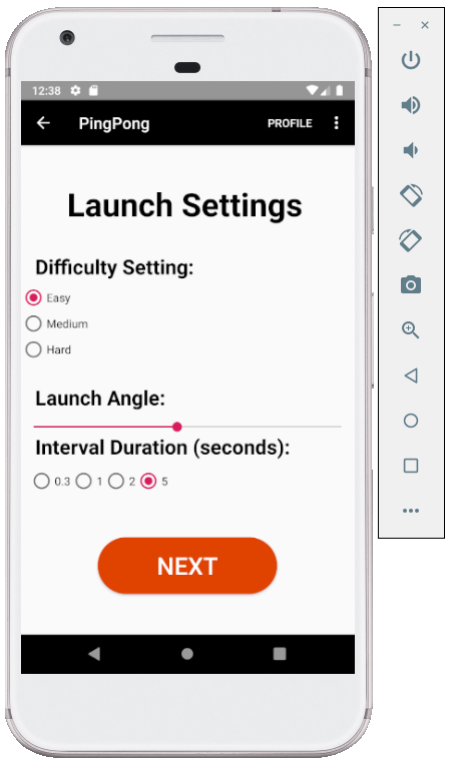
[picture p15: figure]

]

Figure 3: Launch Settings Page

3.2.2 Image/firmware

The firmware is currently being developed on a Raspberry Pi 4. The development

platform is running on the Raspian OS and it is programmed in python language. The

IDE being used for this development is ThonnyPython. The image of Raspian being

used for the development was the one provided by Humber College. It has been set up

to allow remote access, using an Ethernet cable and Ethernet-USB adapter to connect

to any PC or laptop. The Raspian OS image has been configured to allow remote

access and can be accessed using CLI with Putty and using GUI with VNC viewer. The

firmware is developed to control the Servo motor, the solenoid and Dual DC motor

driver. The code for firmware is now an integrated version of the base code for the

prototypes for the given devices. The new firmware was developed using the code for

the dual motor driver as base. The present version is not setup to get the play difficulty

values stored in the firebase by the mobile application. But in the present version of the

code play settings are hard-coded in the code and for a later version, a defined function

can be added to get the values from the firebase periodically and use them to run the

devices to provide a play level according the settings set by the user. The firmware uses

the GPIO and time module from the Raspberry Pi python modules. The GPIO module

functions are used to use the In/Out pins of the Raspberry Pi in BOARD setting. During

the initial setup, 5V outputs are set to turn on the VCCs for the motor driver and the

Servo motor. Also, GPIOs used for the Motor Driver logic and the Solenoid are set to

output and the 3 PWM outputs to control the Servo motor and the two DC motors. The

PWMs are setup to output a 100Hz frequency to provide easy calculation for the value

of Duty Cycle needed for favorable physical output from the DC motors and the Servo

motor. After the setup is completed by making sure that the GPIOs that control the

motors and the solenoid are set to the values of HIGH and LOW as needed to set the

solenoid in position and the directions for the motors are set. There are different functions defined to simulate the different shots for the Ping-Pong ball, serve up the ball

at the given intervals and turn the machine at a variable angle. The firmware runs in a

loop to systematically and periodically, serve up the ball then launch the ball straight.

Then the loop runs while turning the angle periodically and alternating between the

straight shot, top spin and back spin shots. The angle variation is random, ranging

between zero to fifty degrees. For the upcoming version, the defined function needs to

be implemented that periodically updates the currently hard-coded values for angle,

interval and difficulty.

3.2.3 Breadboard/Independent PCBs

The PCB’s were designed using the Fritzing application. In order to start

development on the PCB’s, we first needed to gain familiarity with how to use the

Fritzing application. In order to do so, we got assistance from the teacher, in addition to

watching YouTube tutorials to gain an understanding of Fritzing’s different uses. We first

tested our circuit designs on our Breadboard’s to check for errors and to ensure that

everything was working as intended. Then created the circuit on a breadboard to test

out the voltages and signal outputs to help get an idea on the parameters that were

available to create an optimal design for creating the PCB. After our Breadboard

designs worked, we started to create the PCB designs. For optimal design purposes,

we needed to ensure that the copper wiring that connected to the ports at the top of the

Pi were all arranged on the top layer of the PCB. Likewise, we needed to ensure that

the wiring for all other components were arranged on the bottom layer. During the

design to change the layer for a wiring connection, the bend points were changed to

vias

When planning the PCB for the Servo Motor, the PCB was designed to contain

an LED to confirm that all components were connected properly when the Raspian code

was ran. We also needed to ensure that it contained a 220 Ohm resistor and 2.2 kilo-

Ohm resistor connected in parallel to moderate the current of the circuit that would

ensure the circuit wouldn’t malfunction from too much current. We needed to provide

the circuit with 5V of voltage to give it enough power to operate. Finally, we needed to

ensure three separate ports for the 3 pins of the Servo Motor that would control the

Voltage, Ground, and Pulse wires.

When developing the PCB for the Dual Motor Driver, the PCB was designed to

support the all the Logic controls for the direction controls for the DC motors, using

GPIOs and speed control using the PWM outputs form the Pi. The VCC logic for the

driver used the 5V output from the Pi to enable the driver to control the DC motors. The

PCB supports both the outputs from the motors and an external power supply to provide

the VM (External Voltage) between 6-12V for the motors. All the components, inputs

and outputs have their grounds (GND) connected to the common GND of the Raspberry

Pi.

When developing the PCB for the Solenoid, the PCB was designed to support

external power supply that provides at least 1 Amp current to the solenoid at 6-9V input.

A single GPIO output is used to control the push-pull function by sending LOW-HIGH

signals respectively. The circuit design uses a NPN transistor with 220 Ohm and

2.2kOhm resistors amplify the minimal current from the GPIO signal of the Pi. A diode is

used to block the back current created from the emf created due to the magnetic effect

of the Solenoid.

3.2.4 Printed Circuit Board

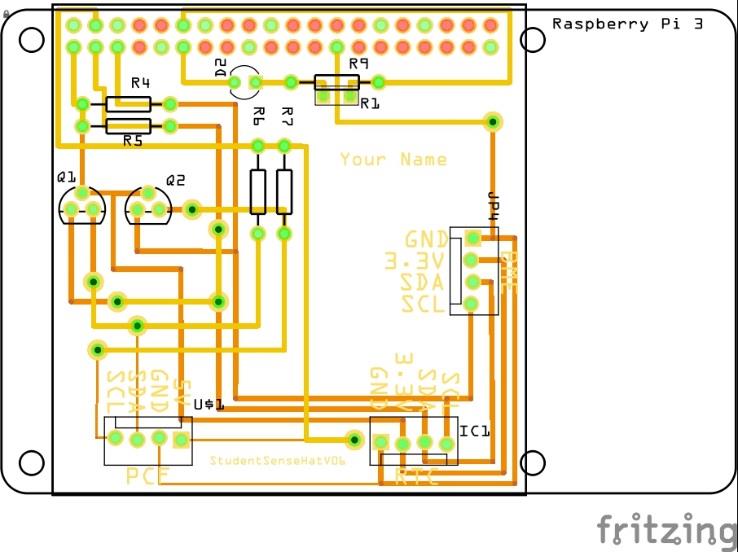
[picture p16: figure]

Figure 5. PCB design This work is a derivative of "http://fritzing.org/parts/" by Fritzing, used under CC:BY-SA 3.0.

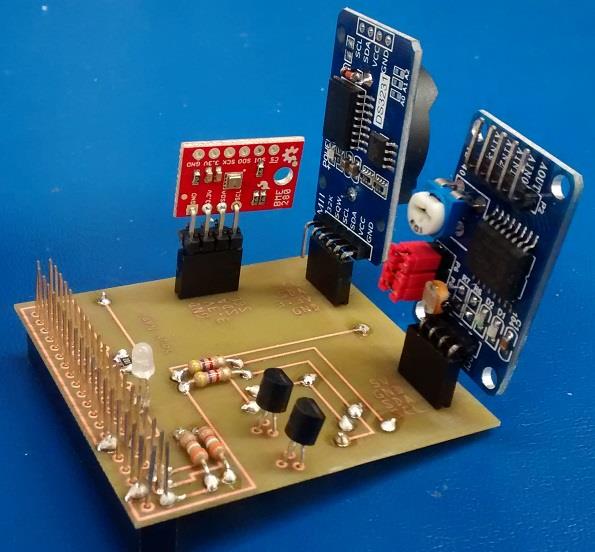
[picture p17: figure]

Figure 6. Humber Sense Hat Prototype PCB.

3.2.5 Enclosure

Demo

/1 Hardware present?

/1 Case encloses development platform and custom PCB.

/1 Appropriate parts securely attached.

/1 Appropriate parts accessible.

/1 Design file in repository, photo in report.

How did you build your Prototype: Case?

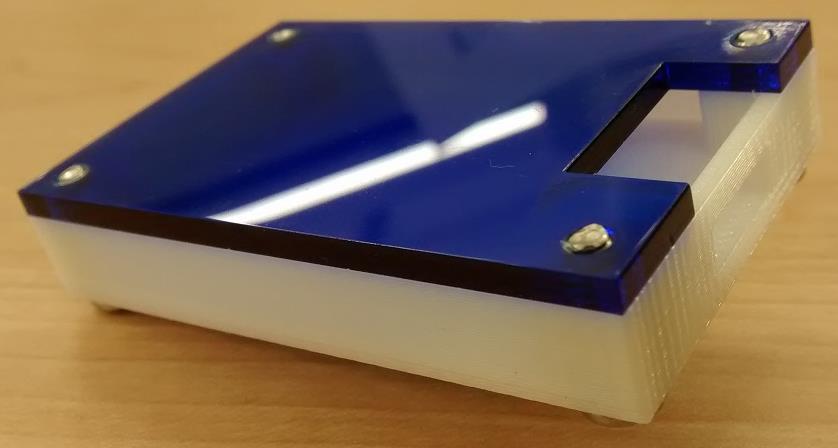
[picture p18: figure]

Figure 7. Example enclosure.
3.3 Integration

Demo

/1 Hardware present?

/1 Data sent by hardware

/1 Data retrieved by mobile application

/1 Action initiated by mobile application

/1 Action recieved by hardware

Report

/1 Enterprise wireless connectivity (250)

/1 Database configuration (250 words)

/1 Security considerations (500 words)

/1 Unit testing (900 words)

/1 Production testing (100 words)

3.3.1 Enterprise Wireless Connectivity

A certificate is created when Wi-Fi is activated that ensure that the device it wants to

connect to is safe for use and will not get hacked. This is a similar process to

connecting a device to a non-local Wi-Fi hotspot, such as at Humber. When the Wi-Fi

system acknowledges that the device is safe for use, it allows the device WiFi access

and full access to all features and data of the Ping-Pong application. The user’s

interaction with the application not only allows full interaction with the machine but also

connectivity to the application’s database without any acknowledgement of the backend

aspects. The firmware on machine is to be set up as the only service running on the Pi

which only sends and receives that from the Firebase account so it make the account

which prevents any harmful data being sent across. So it makes the machine safe to be

connected to the any Home or Private Wi-Fi.

3.3.2 Database Configuration

The database uses email and password verification in both the login and signup

verification screens to give the system additional information about the unique

credentials for each user. Once a new user creates a new account in the signup page,

the database stores the information so that the user can conveniently access the

information when they use the application any sequential times when logging in. The database is hosted by FireBase, a real time database that allows the application’s data

to get transferred back and forth instantaneously. The group decided on using FireBase

as it provided an easy and convenient interface that allows the users to change their

user passwords and email accounts whenever necessary. FireBase is synchronized

with the Ping-Pong Machine in real time to allow for the machine to change it’s launch

characteristics, such as launch angle, launch interval and difficulty settings instantly.

This allows for a convenient play experience for the user as they get to experience the

changes made in the application immediately after they make them. The group decided

on implementing FireStore into our databases as well to allow for storing data that has

to be used over time to show the user their growth over time. With FireStore, we can

create a requirement both through the application and the machine that the database

would only be able to store the user’s latest 30 play sessions. This allows the app

receive the whole play data at a quicker rate as it we can just get the whole collection

soring a user’s data in one go. It also gives the user a more accurate impression of their

progress in using the machine, since they only need to look through their most recent

sessions instead of their full history. Cloud FireStore and Real Time Database allow for

permanent access to the data instead of needing to create extensive backend code for

checking and updating the database data, as they do not implement SQL. Values sent

to the database through to Cloud Firestore include the launch angle, time interval,

difficulty and the timestamp of when the play was used, consisting of both the time and

date.

3.3.3 Security

Whenever a user creates a password when signing up to the application for the first

time, their password gets hashed when it gets stored into the database, getting

reformed into a random series of characters. This process is done by the Authentication

module of Firebase and even the app creators cannot look up a user’s passwords and

the Authentication is marked with a system generated User ID that prevents user’s from

getting into other user’s data. Also None of the user’s can view any login credentials

from FireBase aside from their own. All of these procedures are done in an effort to

prevent user’s from hacking into accounts they wouldn’t otherwise be permitted to use.

Security-wise, FireBase does all the authentication on its own instead of having to

create backend code to enable security and user safety. Firebase Authentication allows

user’s to change their passwords and emails associated to the accounts, so if they feel

that their information is compromised they can move their accounts to completely

different emails but still keep their data about play settings. We can also monitor the

amount data passing through any user’s interaction with the Firabase which is really

small as it only sends some Strings and integers across each time. So if huge chunk of

data is being transmitted then it means, the security of he data has been compromised

and we can close all traffic or traffic from certain accounts to prevent losing any

sensitive data.

3.3.4 Testing

The production testing the machine involves many phases like testing the PCB the

components connected to the PCB the Mechanical fitting of the all the components and

enclosures. But one of the initial testing we can perform for the machine is the it’s connectivity with the database as it takes instructions from the app. For that we don’t

even need to connect all the hardware to the Pi. We can just, instead of running the

firmware for controlling all the components using the data we get from the app. We can

just use the same Firebase connectivity certificate for the machine to run a pseudo code

that can read data from the Real Time Database and just print it as an output. To show

that accurate data is being received by the machine.

## 4.0 Results and Discussions

In regards to the software, our project worked perfectly given that our code worked as it

needed to. Both in terms of the backend connectivity with server and frontend

interaction with the user. The user was able to interact with the database through the

application and their play data was stored for future analysis. Our prototype regarding

the hardware is incomplete as unforeseen circumstances prevented us from getting the

required components from Humber College to fully build the machine. The group

managed to learn quite a bit throughout the process of working on the group project.

Firstly, the group was able to learn to combine all the pertinent hard skills, such as

programming and circuit building, in a more concrete and visibly useful manner. The

group learned how to collaborate and communicate effectively with one another, in

terms of delegating and organizing tasks, in terms of when to get each done, and how

long each task would take in accordance with what the professors outlined in the course

schedule. The need to communicate effectively became even more useful after the

campus closed as there was a necessity to keep one another informed on each other’s

progress verbally and visually through various programs, as we no longer had the

privilege of working together in person. The group was able to organize and update all

pertinent information through Trello, and Github, which served a similar purpose, but

was useful in keeping the professor informed of our progress as well as keeping a

centralized version control of all the documentation, PCB designs, mechanical designs

and source code for both the app and the machine. We also had the privilege

throughout the year of collaborating with an industry professional, Sebastien Dwornik.

We managed to communicate with him regularly through a messaging program, Slack, in addition to regular video conferences to discuss our progress with him. This allowed

him to make recommendations or suggest new ideas to help our project develop in a

more efficient manner, providing us a more nuanced perspective in working in a

professional work environment and improving our communication skills even further. In

terms of developing the actual project, we were able to use various programs such as

Fritzing and Android Studio that managed to expand upon various concepts that we

learned about from previous semesters. Fritzing gave us a more convenient way to

develop and rework our circuits based on schematic criteria using one or more essential

sensors or motors. It also helped immensely with developing Printed Circuit Boards

(PCB’s), as we went from just connecting wires according to circuit design to designing,

building and testing one ourselves. During the project, we had to work concurrently

between creating the code for our sensors and motors and creating the code for our

application. In order to develop the code for the sensors and motors, it was required that

we had to learn basic Python, enforcing the need to keep our minds adaptable and

flexible to be willing to learn new skills as the project went along. We were also able to

expand our knowledge in working with databases as we had to implement databases

with different programs such as Cloud Firestore, in addition to implementing the

necessary code in our Android Studio application code. In order to develop our

application, we used Android Studio, and the Firebase tool supported by it that easily

helped us connect to our Firebase Databases. I felt that the project was an overall

success, barring a few setbacks that occurred from unforeseen circumstances.

## 5.0 Conclusions

The project was started with the idea of mass producing the prototype in mind. It was

designed this way because of the problem specified for the project to be solved was,

making a cheaper and competitive machine and bring it to market. The prototype was

built using the basic components, but was run using advanced and refined methods in

respect of the machines available in the market. The advanced methods like using a

mobile application to control the machine, storing user data in Firebase database to

keep track of progress, and running the machine on a Broadcom platform like the

Raspberry Pi that has higher capabilities in term of memory and processing speed that

are levels higher than simple built PLC chips. These methods were implemented so that

it can accomplish the mark of competitive gameplay, instead of just randomly throwing

balls at the user.

Hence, all the materials used are easily available and can be produced like in a

production line, creating thousands of the different parts separately and assembling

them and packaging them to make a marketable product.

For the goal of keeping the product cheap, the product needed to be based on limited

number of components, but we believe that every product needs to be upgraded after

some time. So, for further progress of the machine, we could still keep improving the

application like, analyzing player history and display the growth in forms of charts and

tables. We could also keep improving the firmware, which can be updated remotely on

already sold machines. The improvements to the machine could entail more complexity

in the process of setting up and launching the ball by adding more spin and lob shots.

Therefore, like all the innovations in history we need to keep improving on this idea and

we may end up creating a device that leads to inspiration for some engineer in the

future generation.

## 6.0 References

13 Best Ping Pong Robots That Will Improve Your Game Instantly. (2020, January 11).

Retrieved from bestpingpongtables:

https://www.bestpingpongtables.review/robot/

Cheng, F. (2018). Build Mobile Apps with Ionic 4 and Firebase: Hybrid Mobile App

Development.

OACETT. (2017, March). I need to Complete a Technology Report. Retrieved from The

Ontario Association of Certified Engineering Technicians and Technologists:

https://www.oacett.org/Membership/Technology-Report-and-Seminar

Robuck, M. (2018, 11). AWS goes deep and wide with machine learning services and

capabilities. Fierceinstaller.

## 7.0 Appendix

7.1 Firmware code

This is the link to our Updated code:

https://github.com/Warris-

Sohi/SmartTennisBallMachine/blob/master/Firmware/SmartTennisFirmware.py (https://github.com/Warris-Sohi/SmartTennisBallMachine/blob/master/Firmware/SmartTennisFirmware.py)

# Maker's Digest

# DC Motor Control with tb6612fng dual h-bridge motor controller ##

from time import sleep | # Import sleep from time
from datetime import datetime
import RPi.GPIO as GPIO | # Import Standard GPIO Module
GPIO.setmode(GPIO.BOARD) | # Set GPIO mode to BCM
GPIO.setwarnings(False);

# PWM Frequency

pwmFreq = 100

# Setup Pins for motor controller

GPIO.setup(7, GPIO.OUT) | # Solenoidcntrl
GPIO.setup(12, GPIO.OUT) | # ServoPWM
GPIO.setup(36, GPIO.OUT) | # AIN2
GPIO.setup(32, GPIO.OUT) | # AIN1
GPIO.setup(37, GPIO.OUT) | # STBY
GPIO.setup(31, GPIO.OUT) | # BIN1
GPIO.setup(33, GPIO.OUT) | # BIN2
GPIO.setup(40, GPIO.OUT) | # PWMA
GPIO.setup(38, GPIO.OUT) | # PWMB
pwmstp = GPIO.PWM(12, pwmFreq) | # pin 18 to PWM
pwmb = GPIO.PWM(38, pwmFreq) | # pin 13 to PWM
pwma = GPIO.PWM(40, pwmFreq)
pwma.start(100)
pwmb.start(100)
pwmstp.start(200)

## Functions

def turnAngle():

pwmstp.ChangeDutyCycle(10) pwmstp.ChangeDutyCycle(20) pwmstp.ChangeDutyCycle(30)

def shoot(spd):
runMotor(0, spd, 1)
runMotor(1, spd, 0)

def topshot(spd1,spd2):
runMotor(0, spd1, 1)
runMotor(1, spd2, 0)

def backshot(spd1,spd2):
runMotor(0, spd1, 1)
runMotor(1, spd2, 0)

def runMotor(motor, spd, direction): GPIO.output(37, GPIO.HIGH); in1 = GPIO.HIGH
in2 = GPIO.LOW

if(direction == 1):
in1 = GPIO.LOW
in2 = GPIO.HIGH

if(motor == 0):
GPIO.output(32, in1)
GPIO.output(36, in2)
pwma.ChangeDutyCycle(spd)
elif(motor == 1):
GPIO.output(31, in1)
GPIO.output(33, in2)
pwmb.ChangeDutyCycle(spd)

def interval()
GPIO.output(7,GPIO.HIGH)
sleep(1)
GPIO.output(7,GPIO.LOW)

def motorStop():
GPIO.output(37, GPIO.LOW)

## Main

def main(args=None):
try:
while True:
interval()
shoot(50) | # run motor forward
sleep(1) | # ... for 2 seconds
motorStop() | # ... stop motor
turnAngle()
interval() | # delay between motor runs
topshot(50,30) | # turn Left
sleep(1) | # ... for 2 seconds
motorStop() | # ... stop motors

turnAngle()
interval() | # delay between motor runs
backshot(30,50) | # turn Right
sleep(1) | # ... for 2 seconds
motorStop() | # ... stop motors
turnAngle()
sleep(2) | # delay between motor runs
except KeyboardInterrupt:
pass
motorStop()
GPIO.cleanup()
if __name__ == "__main__": main()

7.2 Application code

Here is the link to complete application in our repository: https://github.com/Warris-

Sohi/SmartTennisBallMachine/tree/master/Mobile%20App/PiPo (https://github.com/Warris-Sohi/SmartTennisBallMachine/tree/master/Mobile%20App/PiPo)

Login.java:

package com.sppm.pipo;

import androidx.annotation.NonNull;
import androidx.appcompat.app.AppCompatActivity;

import android.content.Intent;
import android.os.Bundle;
import android.text.TextUtils; import android.util.Log;
import android.view.View;
import android.widget.Button; import android.widget.EditText;
import android.widget.Toast;

import com.google.android.gms.tasks.OnCompleteListener; import com.google.android.gms.tasks.Task;
import com.google.firebase.auth.AuthResult;
import com.google.firebase.auth.FirebaseAuth;
import com.google.firebase.auth.FirebaseUser;

public class Login extends AppCompatActivity { EditText email,password;
private FirebaseAuth mAuth;
String Email,Password;
@Override
protected void onCreate(Bundle savedInstanceState) { super.onCreate(savedInstanceState); setContentView(R.layout.activity_login); email=findViewById(R.id.usernameText);

password=findViewById(R.id.passwordText2);
mAuth = FirebaseAuth.getInstance();
final Button button = findViewById(R.id.buttonLogin); button.setOnClickListener(new View.OnClickListener() { public void onClick(View v) {
Email = email.getText().toString().trim(); Password = password.getText().toString().trim(); if (TextUtils.isEmpty(Email)){ Toast.makeText(Login.this, "Enter Email", Toast.LENGTH_SHORT).show(); return;
}else if (TextUtils.isEmpty(Password)){ Toast.makeText(Login.this, "Enter Password", Toast.LENGTH_SHORT).show(); return;
}else if (Password.length()<8) {
Toast.makeText(Login.this, "Password must be greater then 8 characters", Toast.LENGTH_SHORT).show(); return;
}
mAuth.signInWithEmailAndPassword(Email, Password) .addOnCompleteListener(Login.this, new OnCompleteListener<AuthResult>() { @Override
public void onComplete(@NonNull Task<AuthResult> task) {
if (task.isSuccessful()) {
// Sign in success, update UI with the signed-in user's information //Log.d(TAG, "signInWithEmail:success"); FirebaseUser user =
mAuth.getCurrentUser();
updateUI(user);
} else {
// If sign in fails, display a message to the user.
//Log.w(TAG, "signInWithEmail:failure", task.getException());
Toast.makeText(Login.this, "Authentication failed.",
Toast.LENGTH_SHORT).show(); updateUI(null);
}

// ...
}
});
}
});
}

private void updateUI(FirebaseUser fu) { if (fu != null) {
Intent intent = new Intent(Login.this, Play.class); startActivity(intent);}
}

@Override
public void onStart() {
super.onStart();
// Check if user is signed in (non-null) and update UI accordingly. FirebaseUser currentUser = mAuth.getCurrentUser(); updateUI(currentUser);
}

public void onClick(View view) {
Intent intent = new Intent(Login.this, SignUp.class); startActivity(intent);
}
}

MainActivity.java:

package com.sppm.pipo;

import androidx.appcompat.app.AppCompatActivity;

import android.content.Intent;
import android.os.Bundle;
import android.view.View;
import android.widget.Button;

public class MainActivity extends AppCompatActivity {

@Override
protected void onCreate(Bundle savedInstanceState) { super.onCreate(savedInstanceState); setContentView(R.layout.activity_main);
Button button1;
button1 = (Button) findViewById(R.id.Log_In); button1.setOnClickListener(new View.OnClickListener() { @Override
public void onClick(View v) {

Intent intent = new Intent(MainActivity.this, Login.class); startActivity(intent);
}
});

}
public void onClick(View view) {
Intent intent = new Intent(MainActivity.this, SignUp.class); startActivity(intent);
}

}
Play.java:

package com.sppm.pipo;

import androidx.appcompat.app.AppCompatActivity;

import android.content.Intent;
import android.os.Bundle;
import android.view.Menu;
import android.view.MenuInflater; import android.view.MenuItem; import android.view.View;
import android.widget.Button; import android.widget.RadioButton; import android.widget.RadioGroup; import android.widget.SeekBar;
import android.widget.Toast;

import com.google.firebase.auth.FirebaseAuth;

public class Play extends AppCompatActivity { String difficulty="easy";
int LaunchAngle;
int TimeInterval;
RadioButton diff;
RadioGroup radioGroup;
private SeekBar LAseekBar;
private SeekBar IDseekBar;
@Override
protected void onCreate(Bundle savedInstanceState) { super.onCreate(savedInstanceState); setContentView(R.layout.activity_play);
radioGroup = (RadioGroup)findViewById(R.id.RadioGroup); LAseekBar = (SeekBar) findViewById(R.id.LA); IDseekBar = (SeekBar) findViewById(R.id.ID); LAseekBar.setOnSeekBarChangeListener(new SeekBar.OnSeekBarChangeListener() { int progress = 0;

@Override
public void onProgressChanged(SeekBar seekBar, int progresValue, boolean fromUser) {
progress = progresValue;
}

@Override
public void onStartTrackingTouch(SeekBar seekBar) { }

@Override
public void onStopTrackingTouch(SeekBar seekBar) {

}
});
IDseekBar.setOnSeekBarChangeListener(new SeekBar.OnSeekBarChangeListener() { int progress = 0;

@Override
public void onProgressChanged(SeekBar seekBar, int progresValue, boolean fromUser) {

progress = progresValue;
}

@Override
public void onStartTrackingTouch(SeekBar seekBar) { }

@Override
public void onStopTrackingTouch(SeekBar seekBar) { }
});
final Button button = findViewById(R.id.nextButton); button.setOnClickListener(new View.OnClickListener() { public void onClick(View v) {
int selectedId = radioGroup.getCheckedRadioButtonId(); diff=(RadioButton) findViewById(selectedId); if(selectedId==-1){
Toast.makeText(Play.this,"Nothing selected for difficulty", Toast.LENGTH_SHORT).show(); }
else{
difficulty=diff.getText().toString(); }
TimeInterval= IDseekBar.getProgress(); LaunchAngle= LAseekBar.getProgress();

Intent intent = new Intent(Play.this, Start.class); intent.putExtra("difficulty",difficulty); intent.putExtra("TI",TimeInterval); intent.putExtra("LA",LaunchAngle);

startActivity(intent);
}
});
}

public boolean onCreateOptionsMenu(Menu menu) { MenuInflater inflater = getMenuInflater(); inflater.inflate(R.menu.menu1, menu);
return true;
}
public boolean onOptionsItemSelected(MenuItem item) { //respond to menu item selection
switch (item.getItemId()) {
case R.id.Profile:
startActivity(new Intent(this, Profile.class)); return true;
case R.id.Settings:
startActivity(new Intent(this, Settings.class)); return true;
case R.id.SignOut:
FirebaseAuth.getInstance().signOut(); startActivity(new Intent(this, MainActivity.class)); return true;
default:
return super.onOptionsItemSelected(item);
}

}
}
Post.java:

package com.sppm.pipo;

public class Post {
String difficulty;
int LA,TI;
public Post(){}
public Post(String difficulty,int LA,int TI){ this.difficulty=difficulty;
this.LA=LA;
this.TI=TI;
}

public String getDifficulty() { return difficulty;
}

public void setDifficulty(String difficulty) { this.difficulty = difficulty;
}

public int getLA() {
return LA;
}

public void setLA(int LA) { this.LA = LA;
}

public int getTI() {
return TI;
}

public void setTI(int TI) { this.TI = TI;
}
}
Profile.java:

package com.sppm.pipo;

import androidx.annotation.NonNull;
import androidx.appcompat.app.AppCompatActivity;

import android.content.Intent;
import android.os.Bundle;
import android.util.Log;
import android.view.View;
import android.widget.Button; import android.widget.RadioButton; import android.widget.TextView; import android.widget.Toast;

import com.google.android.gms.tasks.OnCompleteListener; import com.google.android.gms.tasks.Task;
import com.google.firebase.auth.FirebaseAuth;
import com.google.firebase.auth.FirebaseUser;
import com.google.firebase.firestore.FirebaseFirestore; import com.google.firebase.firestore.QueryDocumentSnapshot; import com.google.firebase.firestore.QuerySnapshot;

public class Profile extends AppCompatActivity {
private static final String TAG = "CloudFireStore"; TextView idLabel,emailLabel,docText; FirebaseFirestore db = FirebaseFirestore.getInstance(); @Override
protected void onCreate(Bundle savedInstanceState) { super.onCreate(savedInstanceState); setContentView(R.layout.activity_profile);
FirebaseUser user = FirebaseAuth.getInstance().getCurrentUser(); idLabel=(TextView)findViewById(R.id.profileid); emailLabel=(TextView)findViewById(R.id.profile_email); docText=(TextView)findViewById(R.id.docText);
String email = user.getEmail();
String uid = user.getUid();
idLabel.setText(uid);
emailLabel.setText(email);
/*final Button button = findViewById(R.id.button4); button.setOnClickListener(new View.OnClickListener() { public void onClick(View v) { db.collection("users")
.get()
.addOnCompleteListener(new OnCompleteListener<QuerySnapshot>() { @Override
public void onComplete(@NonNull Task<QuerySnapshot> task) {
if (task.isSuccessful()) {
for (QueryDocumentSnapshot document : task.getResult()) {
Log.d(TAG, document.getId() + " => " + document.getData());
String
difficultydata=document.getString("Difficulty"); String
LAdata=document.getString("Launch");
String
TIdata=document.getString("Interval"); String
timedata=document.getString("Timestamp");

docText.setText(difficultydata+";"+LAdata+";"+TIdata+";"+timedata); }
} else {
Log.w(TAG, "Error getting documents.", task.getException());
}
}
});

}
});*/
}
}

SignUp.java:

package com.sppm.pipo;

import androidx.annotation.NonNull;
import androidx.appcompat.app.AppCompatActivity;

import android.content.Intent;
import android.os.Bundle;
import android.text.TextUtils; import android.util.Log;
import android.view.View;
import android.widget.Button; import android.widget.EditText;
import android.widget.Toast;

import com.google.android.gms.tasks.OnCompleteListener; import com.google.android.gms.tasks.Task;
import com.google.firebase.auth.AuthResult;
import com.google.firebase.auth.FirebaseAuth;
import com.google.firebase.auth.FirebaseUser;
import com.google.firebase.auth.UserProfileChangeRequest;

public class SignUp extends AppCompatActivity {
private static final String TAG = "EmailPassword"; private FirebaseAuth mAuth;
EditText fname,lname,email,password,cpassword; String Name,Email,Password;

@Override
protected void onCreate(Bundle savedInstanceState) { super.onCreate(savedInstanceState); setContentView(R.layout.activity_sign_up); mAuth = FirebaseAuth.getInstance(); fname=findViewById(R.id.fnameText); lname=findViewById(R.id.lnameText); email=findViewById(R.id.emailText); password=findViewById(R.id.passwordText); cpassword=findViewById(R.id.cpasswordText);

Button button2;

button2 = (Button)findViewById(R.id.SignUpbutton); button2.setOnClickListener(new View.OnClickListener() { @Override
public void onClick(View v) {
Name = fname+" "+lname;

Email = email.getText().toString().trim(); Password = password.getText().toString().trim();

if (TextUtils.isEmpty(Email)){ Toast.makeText(SignUp.this, "Enter Email", Toast.LENGTH_SHORT).show(); return;
}else if (TextUtils.isEmpty(Password)){ Toast.makeText(SignUp.this, "Enter Password", Toast.LENGTH_SHORT).show(); return;
}else if (Password.length()<8) { Toast.makeText(SignUp.this, "Password must be greater then 8 characters", Toast.LENGTH_SHORT).show(); return;
}
createAccount(Email,Password);

}
});
}
@Override
public void onStart() {
super.onStart();
// Check if user is signed in (non-null) and update UI accordingly. FirebaseUser currentUser = mAuth.getCurrentUser(); updateUI(currentUser);
}

private void updateUI(FirebaseUser currentUser) {
if (currentUser != null) {
Intent intent = new Intent(SignUp.this, Play.class); startActivity(intent);}
}

public void onClick(View view) {
Intent intent = new Intent(SignUp.this, Login.class); startActivity(intent);
}
private void createAccount(String email, String password) { Log.d(TAG, "createAccount:" + email);

// [START create_user_with_email] mAuth.createUserWithEmailAndPassword(email, password) .addOnCompleteListener(this, new OnCompleteListener<AuthResult>() { @Override
public void onComplete(@NonNull Task<AuthResult> task) { if (task.isSuccessful()) {
// Sign in success, update UI with the signed-in user's information
Log.d(TAG, "createUserWithEmail:success"); FirebaseUser user = mAuth.getCurrentUser(); updateUI(user);
} else {

// If sign in fails, display a message to the user.
Log.w(TAG, "createUserWithEmail:failure", task.getException());
Toast.makeText(SignUp.this, "Authentication failed.",
Toast.LENGTH_SHORT).show(); updateUI(null);
}
}
});
// [END create_user_with_email] }

}

Start.java:

package com.sppm.pipo;

import androidx.annotation.NonNull;
import androidx.appcompat.app.AppCompatActivity;

import android.os.Bundle;
import android.util.Log;
import android.view.View;
import android.widget.Button; import android.widget.TextView;
import android.widget.Toast;

import com.google.android.gms.tasks.OnFailureListener; import com.google.android.gms.tasks.OnSuccessListener; import com.google.firebase.database.DatabaseReference; import com.google.firebase.database.FirebaseDatabase; import com.google.firebase.firestore.DocumentReference; import com.google.firebase.firestore.FirebaseFirestore;

import java.sql.Date;
import java.sql.Timestamp;
import java.util.HashMap;
import java.util.Map;

public class Start extends AppCompatActivity {
private static final String TAG = "CloudFireStore"; FirebaseFirestore db = FirebaseFirestore.getInstance(); @Override
protected void onCreate(Bundle savedInstanceState) { super.onCreate(savedInstanceState); setContentView(R.layout.activity_start);
// Write a message to the database
FirebaseDatabase database = FirebaseDatabase.getInstance();
final DatabaseReference dRef = database.getReference("PiPo_DATA"); TextView labeldiff=(TextView)findViewById(R.id.diffLabel); TextView labelLA=(TextView)findViewById(R.id.LALabel);

TextView labelTI=(TextView)findViewById(R.id.TILabel);
Bundle bundle = getIntent().getExtras();
final String difficulty = bundle.getString("difficulty","easy"); final int LA=bundle.getInt("LA",50);
final int TI=bundle.getInt("TI",2); labeldiff.setText("Difficulty="+difficulty); labelLA.setText("Launch Angle="+LA); labelTI.setText("Time Interval="+TI);
int time = (int) (System.currentTimeMillis()); Timestamp tsTemp = new Timestamp(time); String ts = tsTemp.toString();

final Post post =new Post(difficulty,LA,TI);
final Map<String, Object> playpost = new HashMap<>(); playpost.put("Difficulty", difficulty); playpost.put("Launch", LA); playpost.put("Interval", TI); playpost.put("Timestamp",ts);
Button button = findViewById(R.id.LaunchButton); button.setOnClickListener(new View.OnClickListener() { public void onClick(View v) {
Toast toast = Toast.makeText(getApplicationContext(),
| difficulty+TI+LA, Toast.LENGTH_SHORT);

toast.show();
dRef.push().setValue(post);
// Add a new document with a generated ID db.collection("playSettings")
| .add(playpost) .addOnSuccessListener(new

OnSuccessListener<DocumentReference>() {
| @Override public void onSuccess(DocumentReference

documentReference) {
| Log.d(TAG, "DocumentSnapshot added with ID: "
+ documentReference.getId());
| Toast toast =
Toast.makeText(getApplicationContext(), difficulty+TI+LA,
Toast.LENGTH_SHORT);
| } }) .addOnFailureListener(new OnFailureListener() { @Override public void onFailure(@NonNull Exception e) { Log.w(TAG, "Error adding document", e); Toast toast =

Toast.makeText(getApplicationContext(), "Cloud Firestore update failed", Toast.LENGTH_SHORT);
| } });

}
});

}
}

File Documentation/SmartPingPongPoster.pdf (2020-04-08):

# Gurwarris Sohi, Nicolas Cristiano and Shubham Sharma

# Smart Ping Pong Machine

## ACKNOWLEDGEMENTS

- 13 Best Ping Pong Robots That Will Improve Your Game Instantly. (2020, January 11).
- Cheng, F. (2018). Build Mobile Apps with Ionic 4 and Firebase: Hybrid Mobile App Development.
- OACETT. (2017, March). I need to Complete a Technology Report.
- Robuck, M. (2018, 11). AWS goes deep and wide with machine learning services and capabilities. Fierceinstaller.

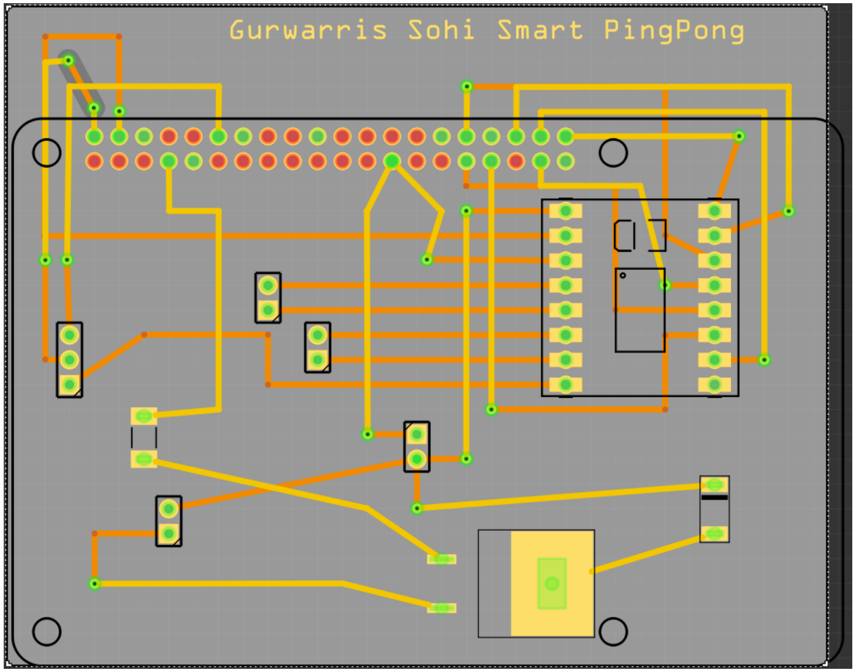
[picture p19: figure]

## TOOLS,PARTS AND FACILITIES

Tools
Equipment like multi-meters, oscilloscopes and function generators accessed from the Humber lab rooms were used to perform the testing required to calibrate outputs needed from the firmware. Software tools like Android Studio for application development, ThonnyPython for firmware development and Firebase to host the databases and act as the connection between the application and the machine were used as well.

Parts
A Raspberry Pi 4 Model B running on RaspianOS was used as the development platform. We used a TB6621FNG Dual Motor driver to control 2 6-9V DC motors to launch Ping-Pong balls, a Push-Pull Solenoid to control launch interval and an ANNIMOS Digital High Torque Servo Motor to control the launcher’s horizontal aim.

Facilities
We used the PCB printing facilities, soldering stations and prototype lab at Humber College to design and create our printed circuit board that contained all mounted components. We also accessed the colleges laser-cutting and 3D printing machines that helped design and create various mechanical components for the machine.

## INTRODUCTION

Our project involves creating a Smart Ping-Pong machine that includes a wide array of play options that provides a wide range of playing styles. This allows for players of different skillsets to improve on their Ping-Pong abilities in a fun and varied manner that can be altered and controlled by a mobile application. In the play application, the user can select their ideal play preferences to give them a comfortable play experience or to ease them into using the machine. We would like to thank our mentor Sebastian Dwornik from PDA for supporting this project.

Background:
Our idea was based on reviewing the designs and features of some of the available machines in the market. These devices proved to be either too costly or provide minimal features and are all controlled by some form of bulky remote with buttons and dials. Moreover, cost-effective machines intended for rookie Ping-Pong players lose their effectiveness after a brief time span as they are constrained by the level of difficulty they can offer. As a result, the player needs to continually spend more money to buy more costly machines to keep up with their improving skill levels.

Idea:
To solve the issues mentioned above, a machine was designed that uses basic and cheaper components to suit a wide array of play styles. This is achieved while the machine is controlled by the application that keeps track of the user’s growth over the period of their machine use.

## ELECTRONICS/PCB, FIRMWARE

Electronics
We initially designed all our components individually, then tested them on the breadboard. When the breadboarded circuits worked with the basic prototype firmware, we advanced to preparing our PCBs. We
used female header sockets to mount the devices to solder and connect all components. This measure was taken to prevent wasting any components on the PCB with errors. This proved to be beneficial as it took a few attempts to fix our component issues. We then advanced to building our Integrated circuit, which has all three components working together to accomplish our machine objectives. The integrated design has the firmware using 2 PWMs to control the speed of the DC motors separately using the Dual motor driver. This can also control the direction the motors rotate horizontally, which gives the user opportunity to rotate the machine both clockwise and counter-clockwise. Another PWM output is used to control the Servo Motor which can rotate in a 270-degree range but only needs to rotate in a 50-degree range. The Servo Motor we use can handle the torque of a 20Kg mass on the axle so it can easily and quickly aim as soon as it receives its instructions. The solenoid uses a basic
ON/OFF switch to pull back the flap that stops the ball to let it go and quickly reverse to stop the next ball(s).

## MOBILE APPLICATION, DATABASE

Mobile Application
The mobile application allows the user to log in if they already have an account. If not, they can access the Sign-Up page to create a new account. The user must fill in data fields such as First Name, Last Name, Email Address, Password, and Password Confirmation. They can then sign in using their Email and Password. Offline verifications are performed to prevent users from having predictable passwords or entering fake email ID’s. The sign up and sign in backend are performed through the Firebase Authentication module. The application recognizes the user and keeps them signed in unless they sign out. After the login, users can select Difficulty, Launch Interval of Balls and Horizontal Angle Range for Launched Shots. They can then access the Launch Page to start their play session after examining their chosen play settings and clicking the play button.

Database
The selected fields are sent to the Realtime Database and the Cloud Firestore. The Realtime Database is used to send information to the Ping-Pong machine to start the play session. The Cloud Firsetore saves information so that the user can view their old settings to observe their growth as it is easy and quick to read large amounts of information in one session.

## ENCLOSURE

We designed an enclosure for the machine launcher that contains the DC motors and the launched ball area. This is basic design fit together using friction fitting after it was laser cut on a 6mm acrylic that provide it with stability and strength to hold the fast and vibrating motors. We also designed a 3D printable case for the Raspberry Pi and the PCB with its mounted components to secure it from harm. We designed a holder on a heightened cylindrical base for the Servo Motor that acts as the base for the launcher; the base is connected to the Raspberry Pi using screws. An old vacuum pipe was going to be used as it was hollow enough to allow the ball pass through. In addition, it would’ve been easy to cut a flap into it to allow the solenoid to control launch intervals.

## CONCLUSIONS

With all these features that we have worked towards during our path of designing and completing this project, we believe that we have created an machine that accomplishes the objective we had in mind. The machine is cheaper, but offers competitive play styles and is connected to and controlled by a mobile app. So after this, our next goal could be to add more functionality to the app like, user’s sharing their stats to their friends to show them their progress or adding horizontal spin mode to the machine to make it even more hard to play against to give the users their money’s worth.

Figure 3: Raspberry Pi 4 – Main Project Development
Platform

Figure 1: Diagram of Finalized Fritzing PCB Design

Figure 2: Servo Motor
used for Horizontal
Launch functionality

Figures 6 and 7: Corell Design and stl designs used model enclosures for both machine casing and launcher

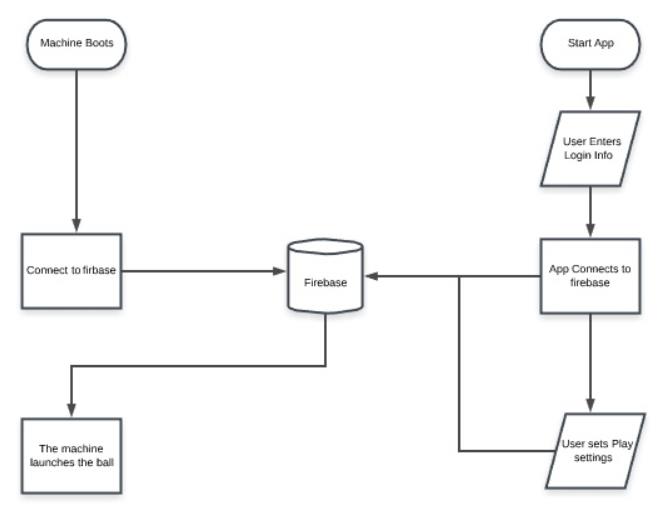
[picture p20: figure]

Figure 4: System Diagram – How Application, Machine and Databases interact with one another

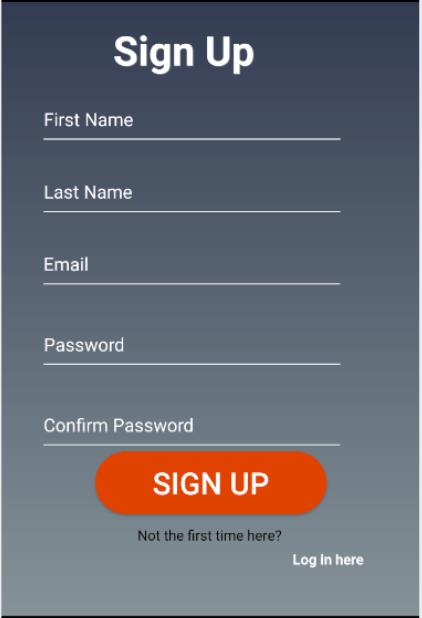
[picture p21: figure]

Figure 5: Sign Up Screen with Required User Credentials

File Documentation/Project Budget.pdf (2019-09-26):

Component | Model | Units | Price(CAD) | Subtotal | Subtotal+Taxes Notes

Raspberry Pi Kit

Raspberry | Pi 4
Model B | 1 | 89 | 89 | 99.68 Ordered

DC motor Driver

SparkFun | Dual
TB6612FNG | 1 | 7.1 | 7.1 | 7.952
To | be
| | | | | Ordered

Servomotor

Blue Tower Pro
SG90 9g Micro
Servo | 1 | 4.48 | 4.48 | 5.0176

Nicolas's
Compone
nt

3D Print Components

Valve, The H BEAM
for DC motors,
hopper | 3 | 15 | 45 | 50.4
To | be
Ordered

Solenoid Valve

SparkFun
ROB011015 | 1 | 7.56 | 7.56 | 8.4672

Sahil's
Compone
nt
Infrared Sensor | GP2Y0A41SK0F | 1 | 10.18 | 10.18 | 11.4016

Sahil's
Compone
nt
Laser-Cutting | For the project
| Case | 2 | 16 | 32 | 35.84
To | be
Ordered
12 V DC Motors | ROB-11696 | 2 | 2.8 | 5.6 | 6.272
To | be
Ordered
Total | 225.0304
| | | | Estimated
| | | | Delivery
costs | 30
| | | | Grand
Total | 255.0304

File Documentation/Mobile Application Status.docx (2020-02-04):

TO: Kristian Medri, Professor, Humber College School of Applied Technology

FROM: Nicolas Cristiano, Computer Engineering Technology Student

Cc: Gurwarris Singh Sohi and Shubham Sharma

DATE: February 4th, 2020

SUBJECT: Ping-Pong Machine Application Status

Research has shown that tennis players, both new and experienced, are using tennis ball machines in order to gain experience and develop their abilities in an effective and efficient manner. Capitalizing on this trend, hardware has been developed for a ping-pong machine, which works largely in the same manner as a tennis machine, only on a smaller scale. Software has also been developed for an application that allows the player to adjust various play factors for how the ping-pong machine operates.

Login Activity

Upon opening the application, the player is required to input their individual data into a signup page. These fields include:

- First Name
- Last Name
- Email
- Password
- Password Confirmation

There are several parameters that need to be achieved for the user to be able to sign up. Most significantly, none of the fields are allowed to be empty. The first name and last name must not have any numbers or special characters (ie ?,!$). The email and password must not have any spaces in between characters. The password must be eight to sixteen characters, and have at least one lowercase letter, one uppercase letter, one special character and one number. The password confirmation must match up perfectly with the password. After the user signs up, they can login for all subsequent sessions, where they only need to input their email and password.

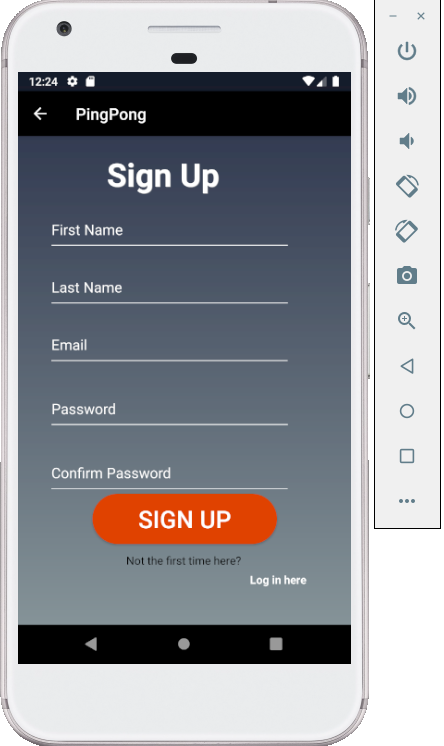
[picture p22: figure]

Figure 1: Sign Up Page

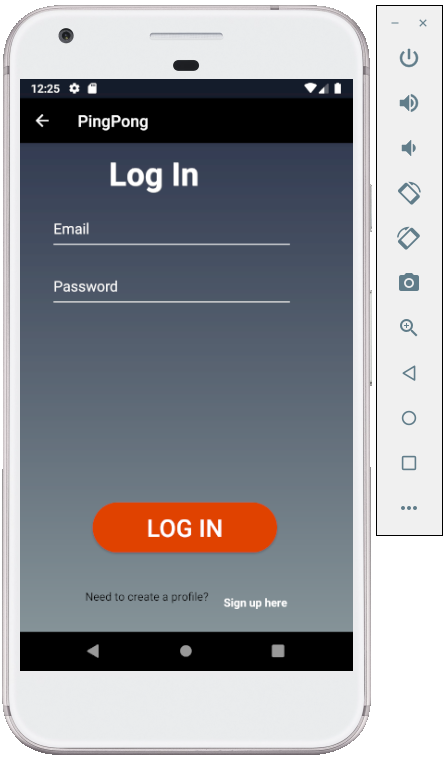
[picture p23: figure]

Figure 2: Login Page

Data Visualization Activity

Once the user logs into the application, they can access a profile page, which displays their first name, last name, email address and a serial number that denotes what machine the given account is linked to. When the user first logs in, the application’s database stores what serial number they have. The profile screen also lets the users access their play settings from the last 30 play sessions.

Action Control Activity

Before the user enters their play session, they can select from a range of play settings. These settings include:

- Difficulty: easy, medium and hard difficulties are selectable, which impact both the launch speed, the range of elevations and type or variation of shots the ping pong balls launch at the user
- Angle: the user can control the horizontal launch angle of the ball from a neutral center position to a 25 degree range, both left and right of the center.
- Launch Interval: the user can control the time interval the balls launch between one another. They can choose between 0.3, 1, 2 and 5 seconds.

If the user does not choose any of their individual settings, they are set to default, which consists of an easy difficulty, a 10-degree launch angle, and 5 second launch interval. Once the user chooses their settings, they can launch their play session in another screen. When launched, the application displays a timer that shows the duration of the play session. If the user wants to change their settings, they need to press the stop button so they can re-access the settings page. They are then able to restart the play session once everything is adjusted to their liking.

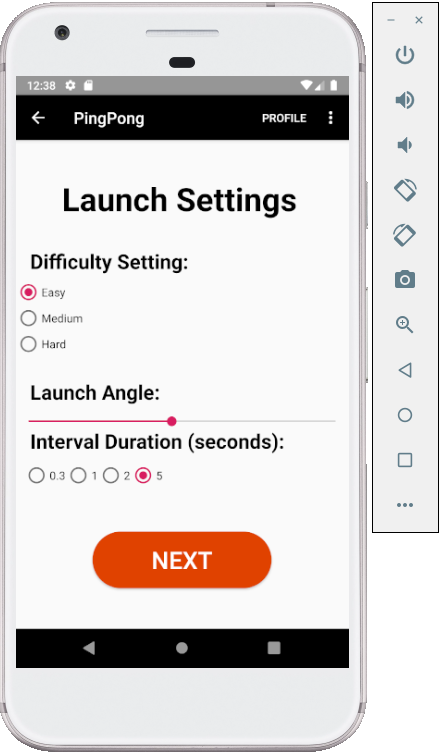
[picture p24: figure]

Figure 3: Launch Settings Page

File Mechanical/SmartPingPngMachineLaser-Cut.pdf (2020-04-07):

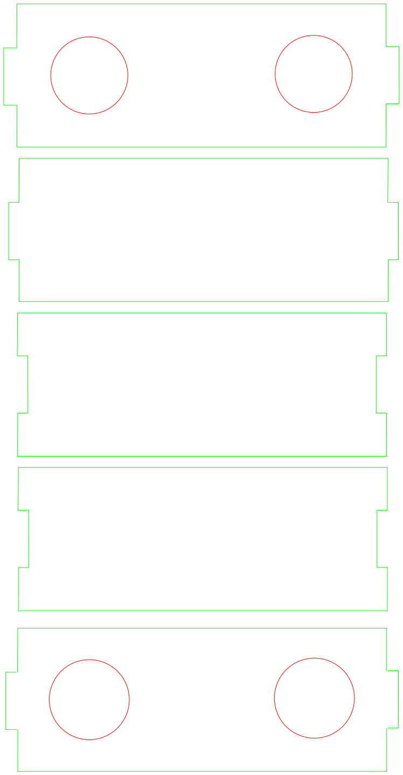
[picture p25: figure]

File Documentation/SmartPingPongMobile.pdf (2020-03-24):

# Mobile Application


Login Activity
Upon opening the application, the player is required to input their individual data into a signup page. These fields include:
- First Name
- Last Name
- Email
- Password
- Password Confirmation

There are several parameters that need to be achieved for the user to be able to sign up. Most significantly, none of the fields can be empty. The first name and last name must not have any numbers or special characters (ie ?,!$). The email and password must not have any spaces in between characters. The password must be eight to sixteen characters, and have at least one lowercase letter, one uppercase letter, one special character and one number. The password confirmation must match up perfectly with the password. After all the above conditions are met, it uses a Firebase Authentication SDK to create a user using the given email and password. After the user signs up, they can login for all subsequent sessions using Firebase method of signing in using the same email and password.

Figure 1: Sign Up Page

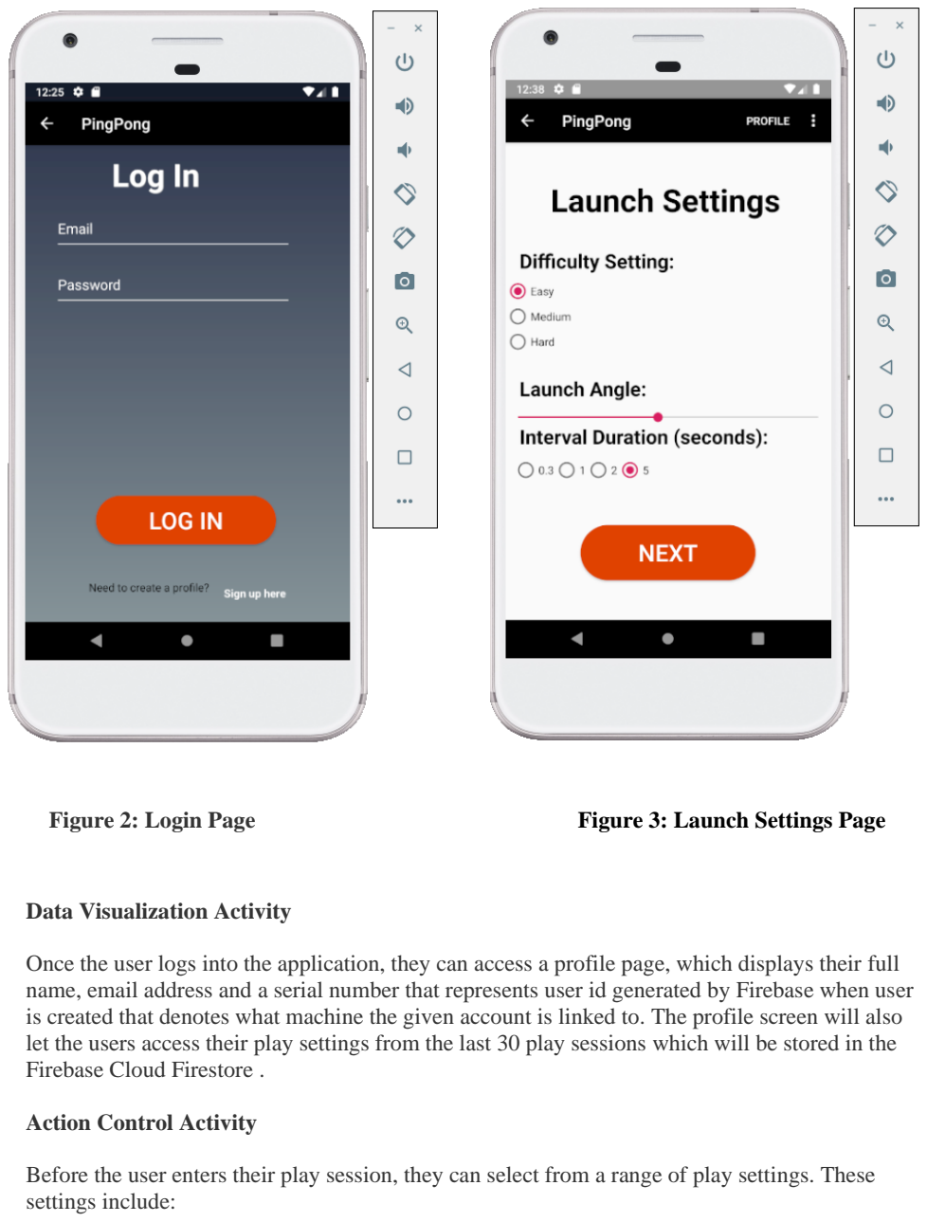
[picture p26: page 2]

Figure 2: Login Page | Figure 3: Launch Settings Page

Data Visualization Activity

Once the user logs into the application, they can access a profile page, which displays their full name, email address and a serial number that represents user id generated by Firebase when user is created that denotes what machine the given account is linked to. The profile screen will also let the users access their play settings from the last 30 play sessions which will be stored in the Firebase Cloud Firestore .

Action Control Activity

Before the user enters their play session, they can select from a range of play settings. These settings include:

- Difficulty: easy, medium and hard difficulties are selectable, which impact both the launch speed, the range of elevations and type or variation of shots the ping pong balls launch at the user
- Angle: the user can control the horizontal launch angle of the ball from a neutral center position to a 25 degree range, both left and right of the center.
- Launch Interval: the user can control the time interval the balls launch between one another. They can choose between 0.3, 1, 2 and 5 seconds.

If the user does not choose any of their individual settings, they are set to default, which consists of an easy difficulty, a 10-degree launch angle, and 5 second launch interval. Once the user chooses their settings, they can launch their play session in another screen. When launched, the application will use a Firebase Real Time Database to send the values to the machine of the play session. If the user wants to change their settings, they need to press the stop button so they can re-access the settings page. They are then able to restart the play session once everything is adjusted to their liking.

Link to our Updated Mobile Application :

https://github.com/Warris-

Sohi/SmartTennisBallMachine/tree/master/Mobile%20App/PiPo (https://github.com/Warris-Sohi/SmartTennisBallMachine/tree/master/Mobile%20App/PiPo)

This is the link to our Updated Report containing the present code in appendix

7.2:

https://github.com/Warris-

Sohi/SmartTennisBallMachine/blob/master/Documentation/ReportTemplate2019-12-

19.docx (https://github.com/Warris-Sohi/SmartTennisBallMachine/blob/master/Documentation/ReportTemplate2019-12-19.docx)

## Grading for this milestone:

/1 Completed: Survey regarding substantial completion of this term /1 Participated: Online session
/2 Login activity
/2 Data visualization activity
/2 Action control activity
/1 Modified Code Files in Appendix /1 Link to Complete Code in Repository

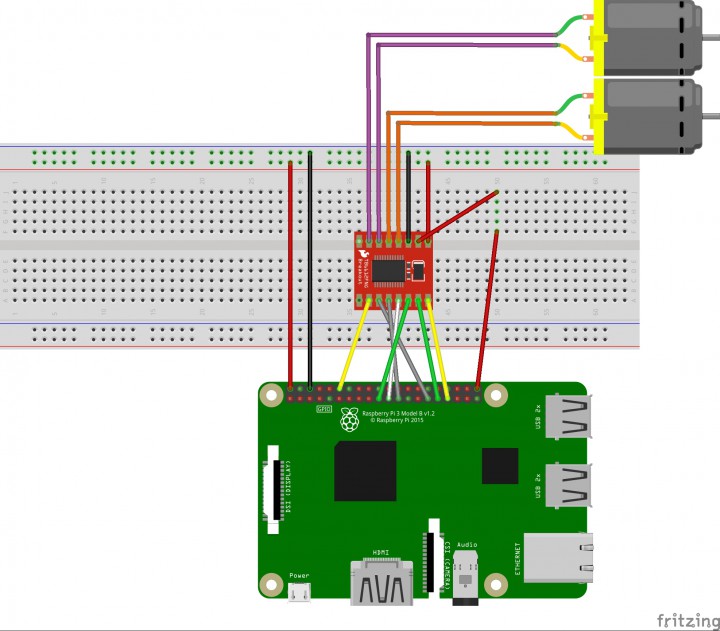
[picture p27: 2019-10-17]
Electronics/DualMotorDriver_bb .jpg

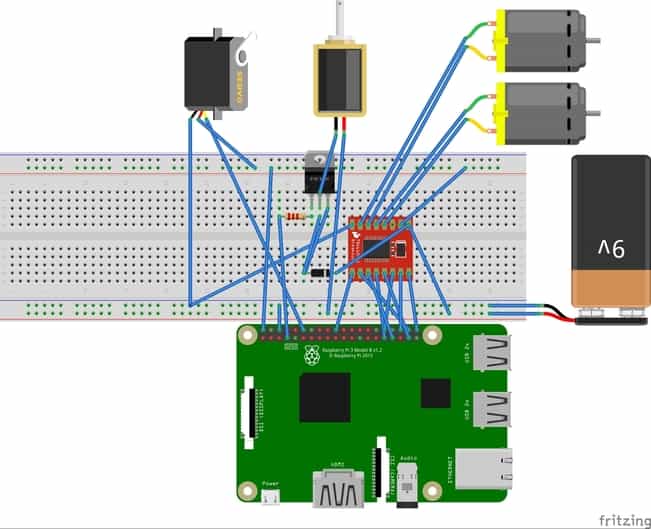
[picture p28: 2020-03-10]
Images/GurwarrisSohi_SmartTennisBallMachine V2_bb.jpg

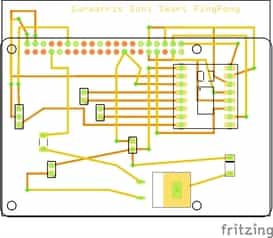
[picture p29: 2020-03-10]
Images/GurwarrisSohi_SmartTennisBallMachine V2_pcb.jpg

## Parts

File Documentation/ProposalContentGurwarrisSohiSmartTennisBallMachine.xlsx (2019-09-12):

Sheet: DataEntry
Submission Date | 2019-09-12
Project Name | Smart Tennis Ball Machine
Student Names | Gurwarris Sohi, Sahil Sahil, and Nicolas Cristiano
Project repository | https://github.com/Warris-Sohi/SmartTennisBallMachine
SensorsEffectors choices | Infrared Sensors, Motion Sensors, Servomotors, Stepper motors
The database will store | Our databases will keep the parameters for each play-type or practice session.
The mobile device functionality will include | The app is gonna be able to set individual parameters, you can save your level of play (level of difficulty). Our just choose one of our presets for difficulty of play.
I will be collaborating with the following company/department | Startup Life
My group in the winter semester will include | Gurwarris Sohi, Sahil Sahil, and Nicolas Cristiano
50 word problem statement | Tennis ball machines today are costly and in the age where every aspect of our life can be remotely controlled from a mobile device, tennis ball machines are still stuck with buttons and 8 bit displays. Present machines are more hardcoded and way less autonomous than today's standards.
100 words of background | Tennis ball machines us a container filled with a number of balls (100 balls by present standards), and then some machine use pressure to launch the ball and at the end a pair of tires placed on either side of the ejection tube either horizontally or vertically to finally launch the ball give the needed spin for each serve type. The whole contraption at the end is moved and horizontally and vertically to aim the ball trajectory. This part only affects the elevation and direction of the ball. But a ball can have same max height and distance with different elevations, with different launch speeds.
Current product APA citation | Baldwin, D. M. (1977). Using the tennis ball serving machine. The Physics Teacher, 15(7), 432–434. doi: 10.1119/1.2339719,
Existing research IEEE paper APA citation | N/A
Brief description of planned purchases | We are planning our machine on a Raspberry Pi 3, which will controll the servo motors that laungh the ball, and also the stepper motors that will aim the ball accordingly and motion sensors to modulate ball speed.
Solution description | Our machine is based on a simpler design than the present machine, which will make the machine cost effective and when the machine is connected to the app, most of the processing is done on the mobile side. So we can have smaller processing size on the machine.

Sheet: DataBase
Submission Date | Project Name | Student Names | Project repository | SensorsEffectors choices | The database will store | The mobile device functionality will include | I will be collaborating with the following company/department | My group in the winter semester will include | 50 word problem statement | 100 words of background | Current product APA citation | Existing research IEEE paper APA citation | Brief description of planned purchases | Solution description
43720 | Smart Tennis Ball Machine | Gurwarris Sohi, Sahil Sahil, and Nicolas Cristiano | https://github.com/Warris-Sohi/SmartTennisBallMachine | Infrared Sensors, Motion Sensors, Servomotors, Stepper motors | Our databases will keep the parameters for each play-type or practice session. | The app is gonna be able to set individual parameters, you can save your level of play (level of difficulty). Our just choose one of our presets for difficulty of play. | Startup Life | Gurwarris Sohi, Sahil Sahil, and Nicolas Cristiano | Tennis ball machines today are costly and in the age where every aspect of our life can be remotely controlled from a mobile device, tennis ball machines are still stuck with buttons and 8 bit displays. Present machines are more hardcoded and way less autonomous than today's standards. | Tennis ball machines us a container filled with a number of balls (100 balls by present standards), and then some machine use pressure to launch the ball and at the end a pair of tires placed on either side of the ejection tube either horizontally or vertically to finally launch the ball give the needed spin for each serve type. The whole contraption at the end is moved and horizontally and vertically to aim the ball trajectory. This part only affects the elevation and direction of the ball. But a ball can have same max height and distance with different elevations, with different launch speeds. | Baldwin, D. M. (1977). Using the tennis ball serving machine. The Physics Teacher, 15(7), 432–434. doi: 10.1119/1.2339719, | N/A | We are planning our machine on a Raspberry Pi 3, which will controll the servo motors that laungh the ball, and also the stepper motors that will aim the ball accordingly and motion sensors to modulate ball speed. | Our machine is based on a simpler design than the present machine, which will make the machine cost effective and when the machine is connected to the app, most of the processing is done on the mobile side. So we can have smaller processing size on the machine.

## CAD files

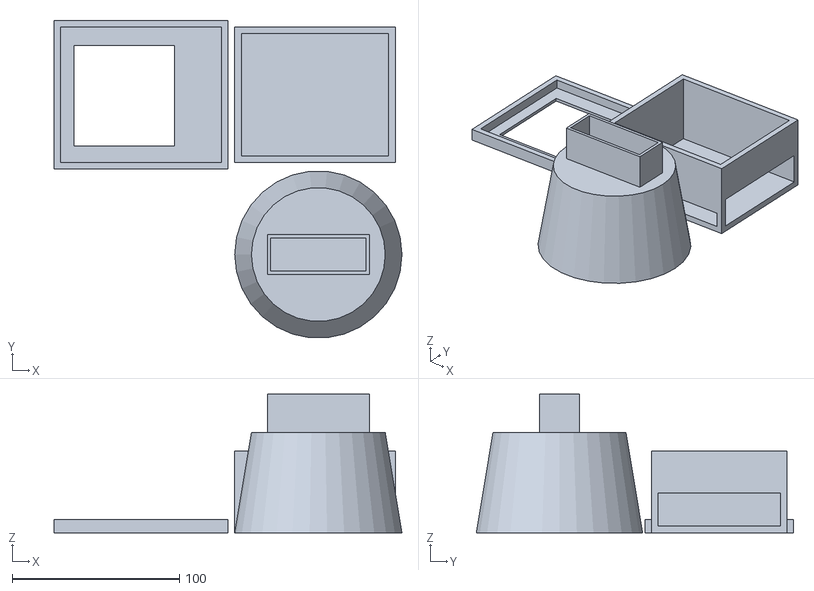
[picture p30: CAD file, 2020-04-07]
Mechanical/SmartPingPongMachine3DComponents.stl
208.0 x 189.7 x 83.0

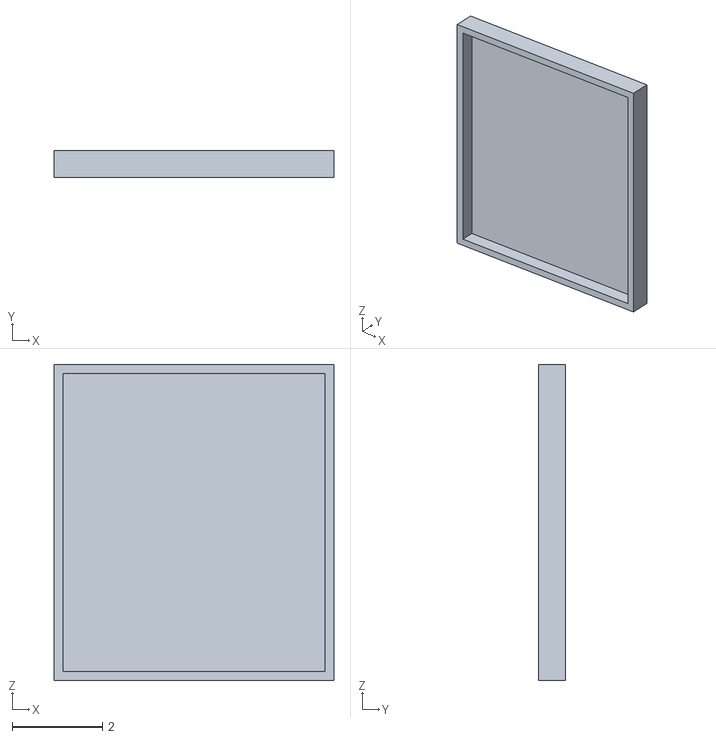
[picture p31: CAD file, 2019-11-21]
Mechanical/Pi Enclosure Lid.stl
6.20 x 0.6 x 7.00

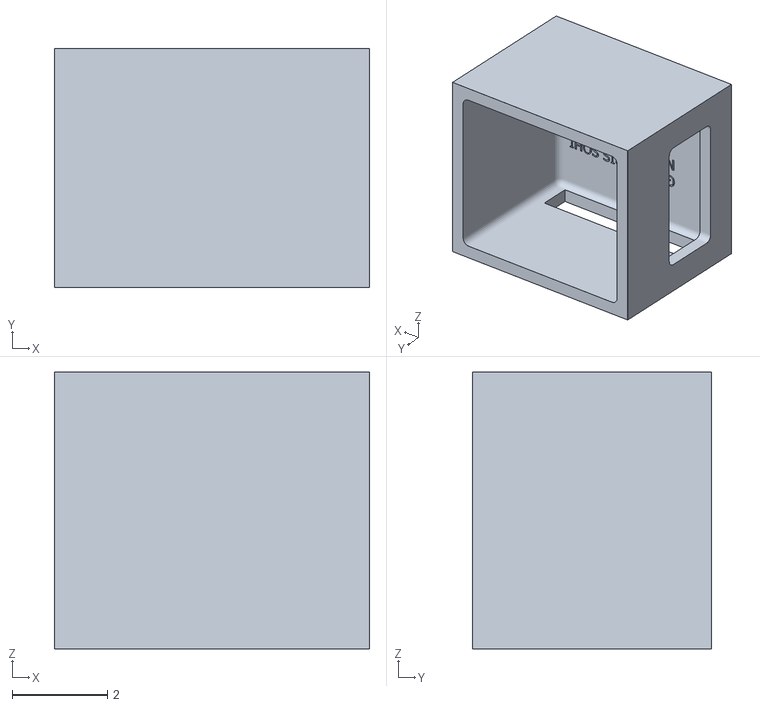
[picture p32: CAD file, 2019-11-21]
Mechanical/Pi Enclosure Base.stl
6.60 x 5.00 x 5.80

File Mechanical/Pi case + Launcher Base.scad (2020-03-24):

difference(){
    cube([96,81,49]);
    //HOLLOW the case
    translate([4,4,4]){
        cube([88,73,45]);
        }
        //HDMI and POWER
    translate([4,0,4]){
        cube([88,4,10]);
        //USB and LAN
    } translate([92,4,4]){
        cube([4,73,20]);
        }   
}
//the Lid
difference(){
    translate([-108,-4,0]){
        cube([104,89,8]);
        }
     translate([-104,0,2]){
        cube([96,81,6]);
        }   
     translate([-96,10,0]){
        cube([60,60,2]);
        } 
    }
union(){
translate([50,-55,0]){
        cylinder(60,50,40);
    }
difference(){
    translate([50,-55,60]){
        cube([61,24,46],center=true);
    }
    translate([50,-55,64]){
        cube([57,20,42],center=true);
    }
}
}

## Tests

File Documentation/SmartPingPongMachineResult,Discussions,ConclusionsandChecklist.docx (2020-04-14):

# 4.0 Results and Discussions

In regards to the software, our project worked perfectly given that our code worked as it needed to. Both in terms of the backend connectivity with server and frontend interaction with the user. The user was able to interact with the database through the application and their play data was stored for future analysis. Our prototype regarding the hardware is incomplete as unforeseen circumstances prevented us from getting the required components from Humber College to fully build the machine. The group managed to learn quite a bit throughout the process of working on the group project. Firstly, the group was able to learn to combine all the pertinent hard skills, such as programming and circuit building, in a more concrete and visibly useful manner. The group learned how to collaborate and communicate effectively with one another, in terms of delegating and organizing tasks, in terms of when to get each done, and how long each task would take in accordance with what the professors outlined in the course schedule. The need to communicate effectively became even more useful after the campus closed as there was a necessity to keep one another informed on each other’s progress verbally and visually through various programs, as we no longer had the privilege of working together in person. The group was able to organize and update all pertinent information through Trello, and Github, which served a similar purpose, but was useful in keeping the professor informed of our progress as well as keeping a centralized version control of all the documentation, PCB designs, mechanical designs and source code for both the app and the machine. We also had the privilege throughout the year of collaborating with an industry professional, Sebastien Dwornik. We managed to communicate with him regularly through a messaging program, Slack, in addition to regular video conferences to discuss our progress with him. This allowed him to make recommendations or suggest new ideas to help our project develop in a more efficient manner, providing us a more nuanced perspective in working in a professional work environment and improving our communication skills even further. In terms of developing the actual project, we were able to use various programs such as Fritzing and Android Studio that managed to expand upon various concepts that we learned about from previous semesters. Fritzing gave us a more convenient way to develop and rework our circuits based on schematic criteria using one or more essential sensors or motors. It also helped immensely with developing Printed Circuit Boards (PCB’s), as we went from just connecting wires according to circuit design to designing, building and testing one ourselves. During the project, we had to work concurrently between creating the code for our sensors and motors and creating the code for our application. In order to develop the code for the sensors and motors, it was required that we had to learn basic Python, enforcing the need to keep our minds adaptable and flexible to be willing to learn new skills as the project went along. We were also able to expand our knowledge in working with databases as we had to implement databases with different programs such as Cloud Firestore, in addition to implementing the necessary code in our Android Studio application code. In order to develop our application, we used Android Studio, and the Firebase tool supported by it that easily helped us connect to our Firebase Databases. I felt that the project was an overall success, barring a few setbacks that occurred from unforeseen circumstances.

# 5.0 Conclusions

The project was started with the idea of mass producing the prototype in mind. It was designed this way because of the problem specified for the project to be solved was, making a cheaper and competitive machine and bring it to market. The prototype was built using the basic components, but was run using advanced and refined methods in respect of the machines available in the market. The advanced methods like using a mobile application to control the machine, storing user data in Firebase database to keep track of progress, and running the machine on a Broadcom platform like the Raspberry Pi that has higher capabilities in term of memory and processing speed that are levels higher than simple built PLC chips. These methods were implemented so that it can accomplish the mark of competitive gameplay, instead of just randomly throwing balls at the user.

Hence, all the materials used are easily available and can be produced like in a production line, creating thousands of the different parts separately and assembling them and packaging them to make a marketable product.

For the goal of keeping the product cheap, the product needed to be based on limited number of components, but we believe that every product needs to be upgraded after some time. So, for further progress of the machine, we could still keep improving the application like, analyzing player history and display the growth in forms of charts and tables. We could also keep improving the firmware, which can be updated remotely on already sold machines. The improvements to the machine could entail more complexity in the process of setting up and launching the ball by adding more spin and lob shots.

Therefore, like all the innovations in history we need to keep improving on this idea and we may end up creating a device that leads to inspiration for some engineer in the future generation.

Prescreening Checklist

1. Has a Proposal for a Technology Report been submitted and accepted and a copy of the approved proposal included in the Technology Report?

Yes

2. Has the Technology Report been submitted within one year since the proposal was approved?

Yes

3. Is the Technology Report consistent with the Proposal (as approved and with the comments and suggestions made by the proposal reviewer)?

Yes

4. Is the Technology Report typed, double-spaced and justified left?

Yes

5. Has a 12 point Arial, Univers, or similar Sans Serif font been used?

Yes

6. Is the body of the report a minimum of 3,000 words?

Yes

7. Are the components included and in the following order: Title Page; Declaration of Authorship; Approved Proposal; Abstract/Executive Summary; Table of Contents; Lists of Illustrations/Diagrams; Body of the TR; Conclusion(s), and if applicable Recommendation(s); Bibliography/Technical References; and Appendices?

Yes

8. Is there a signed Declaration of Authorship?

The declaration of authorship is not signed.

9. Is the report dated?

Yes, it is dated to 14 January, 2020

10. Is the Technology Report current? (The Technology Report should be less than 5 years old.)

Yes

11. Is there a Title Page?

Yes

12. Is there a Table of Contents?

Yes

13. Does the Table of Contents correctly reflect the Components: Headings, Illustrations/Diagrams and Appendices?

Yes

14. Are the pages numbered with appropriate page breaks?

Yes

15. Is there an Abstract/Executive Summary and Introduction?

Yes

16. Does the body of the report contain Section Headings?

Yes

17. Are there Conclusion(s), and if applicable, Recommendation(s)?

Yes

18. Is there a Bibliography with appropriately cited Technical References?

Yes

Report Mechanics and Structure Checklist

This section evaluates the structure, formatting and writing techniques used in the TR. Fulfillment of this criteria leads to a TR that looks professional, is easy to read and is representative of the formatting standards of the industry.

1. Does the Title, in ten words or less, inform readers of the precise subject matter contained in the TR? A title should be concise and include key words for indexing.

Yes, Smart Ping Pong Machine.

2. Does the Abstract or Executive Summary provide a brief overview of the report in approximately 75 to 100 words?

The Executive Summary is 177 words.

3. Does the Abstract or Executive Summary summarize the Conclusion(s), and if applicable, the Recommendation(s)?

The Executive Summary contains the recommendations for how to bring the finished product to market and concludes with some ideas to discover for the machine to after the prototype discussed in the report is completed.

4. Does the Introduction state the reason the work was undertaken? What is the industry, organization or context? What is the problem?

Yes, it talks about the group members who contributed to this project, under the mentorship of Sebastian Dwornik. The introduction also mentions the idea behind the machine to solve a problem of high cost and lack of features in the products in the sports market currently.

5. Does the Introduction cover the scope of the report? What is included and /or admitted, and what procedures are used?

The Introduction specifies the scope of the project in terms of features that are to presented for the machine and the mobile application associated with the machine. It talks about the methods we used to work on the project ranging from softwares we used for research and working on the app to tools used to create the hardware for the machine.

6. Do the headings and subheadings in the Body adequately and accurately describe the section or subsection content?

Yes, each heading and sub-heading is there for all the small considerations to made for the various features and components of the project.

7. Does the Body include information regarding the methodology? Does it indicate materials, equipment and procedures used and why they were selected over alternatives? Is there sufficient detail so that that the methodology can be duplicated by others?

The body of the TR contains information on the steps to re-create the project including the materials used for each step. For some cases, it also has some key pointer to look after like some hints that are not obvious and could take up lot of time if missed, but also quicken the progress of reproduction if taken care of. The body also specifies details on how to sufficiently create and test the product when mass-producing it. The firmware code for the machine and the hardware are also present in the appendices.

8. Does the Body include recent research findings?

Yes, the research is in regards to the motion of the throw to get ideas for what features to create for the machine and how to create them. The research was also in regards to previous products to highlight the shortcoming of the original products in the market.

9. Does the Body include results/data from the study?

The idea and the mechanics for the launcher for the machine is based on a study that is referenced in the report. The study is about factors involving the ball across a distance and adding factors to it, like spins and lobs with respect to the number wheels used and the size and weight of the ball thrown.

10. Are illustrations, tables, diagrams and charts clearly drawn, labelled and numbered?

Yes, illustrations of how the mobile application looks and the designs for the electric components for the machine are used in the report.

11. Is each Conclusion, and if applicable, each Recommendation, stated in a separate paragraph and in a positive way? Conclusions should not be qualified with “it seems”, “probably”, “it may be”, or other words that dilute the strength of the conclusion.

Yes.

12. Are the References/Bibliography complete? All materials referenced in the TR should be represented in the list of References/Bibliography.

Yes, the references are complete.

13. Do the Appendices support the study? Do the Appendices include substantiating data and calculations? Extraneous material should not be included.

The appendices contain code that is used to run all the various components of the machine and also create and manage the database from the app.

14. Is the spelling correct? Has either the Canadian or USA spelling system been used consistently through the TR. Is the language free of jargon? Are acronyms properly introduced? Are abbreviations appropriate and correct? Can someone without specific expertise in the field read and understand the TR?

Yes.

15. Is the same voice (I, one, person, etc.) used consistently throughout the Technology Report? There should not be any switching from third person to first person or vice versa.

As the project was a collective measure by three people the report, so the report is made from that viewpoint and that is signified from the use of the pronoun “We”.

16. Do the grammar and punctuation follow normally accepted rules of use? Use Ron Blicq’s text Technically Write or a similar grammar reference as a guide.

Yes.

17. Are thoughts and illustrations/diagrams/charts that do not belong to the writer properly identified and footnoted in the text? Are quotations indicated correctly? Are the authors referenced in footnotes and/or reference list? Do they include the author’s name, the title of the article/book, the date of publication, and the publisher?

Yes.

Report Content

This section evaluates the quality of the work completed when addressing the problem statement/hypothesis. Fulfillment of these criteria leads to a TR that makes a contribution to the field under study.

1. Are the Problem Statement and Hypothesis significant to the current state of the field/industry?

Yes.

2. Is the Methodology scientifically sound?

Yes. The methodology was created following the scientific process of designing, testing and finalizing the prototype that was born from an initial idea.

3. Are the engineering technology and applied science principles used in the Methodology and Analysis appropriate to the subject area?

Yes.

4. Are the Data and/or Results complete?

No, the project was halted due to the COVID-19 outbreak and the progress was only made to the application and the database side of the project so the data for the methodology is incomplete in regards to the electric and mechanical aspects of the project. For the incomplete aspects, only the simulated designs are provided not their tested outcomes.

5. Have the Mathematical formulae been applied appropriately?

The mathematic calculations for this project were the part of the firmware where calculations were to be performed on based of the data received by the machine from the database. And these calculations were applied according to need to output accurate signals to the machine components.

6. Are the Mathematical calculations done correctly and accurately?

Yes, the calculations were done accurately as they were needed to be accurate for the machine to work. For example, in the case of the Servo motor, if the calculations were wrong in calculating the PWM, instead of just going to the wrong angle the servo could also end up getting overdriven and break the gears in it.

7. Are the Illustrations/Diagrams/Charts technically correct?

Yes.

8. Is the Analysis of the results correct? Is the Analysis complete?

The results conclude that the machine that was proposed in the report, with all the mentioned features was created. From the actual results, one can believe that methodology given the report can theoretically be used to build the said machine. So, Yes, the Analysis of the results is correct.

But it may still be lacking, as it could not actually test the machine with a live participant, which could have concluded the proposed product in its completion.

9. Are the Conclusion(s), and if applicable the Recommendation(s), free of discussion, explanation and opinion?

The conclusions mention that the project has been completed and can be mass-produced using the methodology presented. But they also provide the group’s opinion on further development of the product.

10. Do the Conclusion(s), and if applicable the Recommendation(s), relate to and resolve the Problem Statement and/or Hypothesis?

Yes, the conclusions talk about ideas for further development of the product. And these ideas are for the software side not the hardware side, so no more rise in production cost, but still making the machine with abundant features at the same low cost. This was already the problem the project set out to resolve.

11. Are the Conclusion(s), and if applicable the Recommendation(s), logical?

Yes, the given conclusions are made upon the logical reasoning that the machine accomplishes its task, while solving the problem mentioned the report. Also, it is of sound logic that one would want to upgrade their product further, which is the second part of the conclusions.

12. Does the report make a contribution to the industry/field of study?

Yes.

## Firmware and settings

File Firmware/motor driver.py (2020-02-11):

from time import sleep      # Import sleep from time
import RPi.GPIO as GPIO     # Import Standard GPIO Module

GPIO.setmode(GPIO.BOARD)      # Set GPIO mode to BCM
GPIO.setwarnings(False);

# PWM Frequency
pwmFreq = 100

# Setup Pins for motor controller
GPIO.setup(12, GPIO.OUT)    # PWMA
GPIO.setup(18, GPIO.OUT)    # AIN2
GPIO.setup(16, GPIO.OUT)    # AIN1
GPIO.setup(22, GPIO.OUT)    # STBY
GPIO.setup(15, GPIO.OUT)    # BIN1
GPIO.setup(13, GPIO.OUT)    # BIN2
GPIO.setup(35, GPIO.OUT)    # PWMB

pwma = GPIO.PWM(12, pwmFreq)    # pin 18 to PWM  
pwmb = GPIO.PWM(35, pwmFreq)    # pin 13 to PWM
pwma.start(100)
pwmb.start(100)

## Functions
###############################################################################
def forward(spd):
    runMotor(0, spd, 1)
    runMotor(1, spd, 0)

def turnLeft(spd1,spd2):
    runMotor(0, spd1, 1)
    runMotor(1, spd2, 0)

def turnRight(spd1,spd2):
    runMotor(0, spd1, 1)
    runMotor(1, spd2, 0)

def runMotor(motor, spd, direction):
    GPIO.output(22, GPIO.HIGH);
    in1 = GPIO.HIGH
    in2 = GPIO.LOW

    if(direction == 1):
        in1 = GPIO.LOW
        in2 = GPIO.HIGH

    if(motor == 0):
        GPIO.output(16, in1)
        GPIO.output(18, in2)
        pwma.ChangeDutyCycle(spd)
    elif(motor == 1):
        GPIO.output(15, in1)
        GPIO.output(13, in2)
        pwmb.ChangeDutyCycle(spd)


def motorStop():
    GPIO.output(22, GPIO.LOW)

## Main
##############################################################################
def main(args=None):
    try:
        while True:
            forward(50)     # run motor forward
            sleep(10)        # ... for 2 seconds
            motorStop()     # ... stop motor
            sleep(.25)      # delay between motor runs

            turnLeft(50,30)    # turn Left
            sleep(2)        # ... for 2 seconds
            motorStop()     # ... stop motors
            sleep(.25)      # delay between motor runs

            turnRight(30,50)   # turn Right
            sleep(2)        # ... for 2 seconds
            motorStop()     # ... stop motors
            sleep(2)        # delay between motor runs
    except KeyboardInterrupt:
        pass
        motorStop()
        GPIO.cleanup()
if __name__ == "__main__":
    main()

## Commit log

2019-09-05 Changes Made on 5 Sept, 2019
    [Project Budget.xlsx, Schedule.xlsx]
2019-09-12 Proposal Changes 12-09-2019
    [ProposalContentGurwarrisSohiSmartTennisBallMachine.xlsx]
2019-09-12 Changes 12-09-2019
    [ProposalContentGurwarrisSohiSmartTennisBallMachine.xlsx]
2019-09-19 Update Schedule
    [Schedule.xlsx]
2019-10-17 Breadboard and PCB Design for my dual motor driver
2019-11-07 Create EffectorCode.py
    This is the code for dual motor control
2019-11-14 Add files via upload
    New updated firmware code, that has 3 modes, instead of one.
    1. both motors running at same speed.
    2. motor b running at almost half the speed.
    3. motor a running at almost half the speed.
2019-11-21 Add files via upload
    2 .cdr files containing the specs for my enclosure for my raspberry pi and pcb.
2020-03-10 Integrated PCB design
    [GurwarrisSohi_SmartTennisBallMachine .fzz]
2020-03-10 Integrated PCB breadboard and PCB
2020-03-24 Updated Report with Application Code in Appendix.+Assembly Files
    [Pi case + Launcher Base.scad]
2020-04-07 pull to another device
